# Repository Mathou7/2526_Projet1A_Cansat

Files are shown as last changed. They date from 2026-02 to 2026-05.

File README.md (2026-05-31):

# 2526_Projet1A_Cansat

## A Propos de la CanSat
Le concours CanSat, organisé chaque année dans le cadre du C’Space par le CNES et Planète Sciences, propose aux étudiants de concevoir, construire et faire voler un véritable mini-satellite de la taille d’une canette.
Lancé depuis un drone à environ 150 mètres d’altitude, le CanSat doit réaliser une mission scientifique ou technique en chute contrôlée, tout en respectant des contraintes strictes de taille, de masse et d’autonomie et en réalisant les missions imposées.
Ce concours permet aux étudiants d’aborder concrètement l’ensemble des étapes d’un projet spatial : conception système, intégration électronique, programmation embarquée, gestion de l’énergie et tests.

# L'équipe
- Marin.P
- Pierre-Antoine.R
- Lucas.G
- Arnaud.M
- Mathis.B.

## Liste des fonctionnalités
- Mesure de la pression grâce au baromètre
- Mesure de la distance grâce au TOF
- Utilisation d'un moteur pour actionner un mécanisme
- Prise de vidéo à l'aide de la caméra
- Interrupteur général permettant d'allumer et éteindre la canette

## Choix des composants
- Microcontroleur (stm32g431kbt)
- Baromètre (bnp581)
- Moteur brushless (GA12-N20)
- Centrale inertielle (abandonné) 
- Time of Lights (abandonné)
- Caméra (VC0706)
- Interrupteur

## PCB


PCB à quatre couches constitué de
- STM32G431KBT
- Régulateur 6.5-36V vers 5V
- Régulateur 5V vers 3.3V
- Driver Moteur
- Baromètre
- Interface Jack
- Interface Moteur
- Interface Bouton
- Interface Camera
- Connecteur ST

## Difficultés

Approvisionnement en composants
Nous n'avons pas reçu exactement les composants que l'on souhaitait au départ notamment la caméra qui devait enregistrer les images pendant la chute. Celle à laquelle nous avons eu accès transmet les images par onde radio, permettant de voir directement les images sur un écran extérieur à la canette.

Forme restrictive
La forme particulière du PCB imposée par le volume restreint de la canette et le système d'ouverture du parachute a constitué un frein considérable à la conception du PCB.

Code
Une étude détaillée du fonctionnement du baromètre a été nécessaire afin de coder les différentes fonctions permettant d'aboutir au calcul de l'altitude, ce qui a été très chronophage 

Conception de la canette
Le système d'ouverture du parachute a été le principal défi de conception nous forçant à modifier l'architecture de notre canette.

## Solutions trouvées

Les composants 
Pour la caméra nous avons trouvé une caméra avec un fonctionnement différent de celle initialement prévue.
Nous avons reçu le baromètre déjà soudé sur un PCB alors que nous avions demandé le baromètre seul, nous l'avons donc désoudé pour le resouder sur notre PCB.
En attendant la livraison du connecteur pour la batterie (JST-SH) nous avons soudé directement la batterie à l'interface prévue initialement pour le connecteur.

Conception de la canette 
Nous avons séparé notre canette en 2 espaces : une partie acceuillant le PCB et ses différents composants dont le moteur et une partie dans laquelle se trouve le parachute.
Le système d'ouverture fonctionne gràce à 2 goupilles qui maintiennent la partie contenant le parachute et la patie contenant le PCB ensemble. Ces 2 goupilles sont reliées par des fils au moteur qui en tournant va enrouler ces fils autour de son axe et les libérer. Le capuchon dans lequel se trouve le parachute va donc se détacher pour laisser le parachute sortir et se déployer. Le capuchon une fois détaché du reste de la canette reste relié à celle-ci via un autre fil nous permettant de respecter une exigeance imposée par le concours: aucune partie de la canette ne doit tomber au sol sans être ralentie.

## Partie Méca

Partie contenant le PCB et tout les éléments qui y sont reliés :


Opercule fermant la partie PCB qui maintient la partie parachute :


Corps du capuchon contenant le parachute : 


Opercule fermant le capuchon du parachute :


## Bilan des fonctionnalités

Test du bouton permettant d'allumer la LED

https://github.com/user-attachments/assets/89bd5818-fe06-4b41-a8be-61a60c13a220

Test du moteur

https://github.com/user-attachments/assets/85a999e9-10d9-4074-9609-f378fe4b467d

## Reflexion responsable 
Dans quelle mesure votre projet peut-il être intégré à des mesures d’adaptaton ou d’aténuaton du changement
climatque ?

Notre Cansat pourrait filmer un territoire pendant le largage et nous y montrer une évolution. Par exemple, face à une forêt, voir l'effet d'une déforestation ou d'une dégradation du territoire.

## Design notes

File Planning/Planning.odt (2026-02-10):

Planning

### Déjà fait :

Prototype de cannette utilisable : couvercle avec accroche parachute

parachute fabriquer(à améliorer possiblement)

idées pour ouvertures parachutes

carte STM déjà trouvé

composants choisi(à raffiner quand même pour les références)

### À venir :

-Semaine du 09/02-15/02 :

- Regrouper tous les composants
- Finaliser le schéma fonctionnel
- réussir à faire fonctionner les différents composants
  - obtenir des infos du baromètre, faire tourner les moteurs etc
- Avoir le nouveau modèle de la cansat (changements des tailles des 2 parties)

-Semaine du 16/02-22/02 :

- Si trop gourmand la semaine dernière : faire les tâches laissées en suspend
- voir le modèle du parachute ?
- Si possible faire un schématique complet
  - matériel exact et composant externe(résistance, condendateur, etc)
  - ne pas oublier de mettre des leds
- Kicad
  - finaliser schématique
- avoir un code fonctionnel pour le moteur
- tester l’un des 2 systèmes d’ouverture de parachute au moins

-Vacances du 23/02-08/03 :

- avoir un code qui regroupe le plus de composant sur Github
- Avancer le plus possible sur le routage

-Semaine du 02/03-08/03 :

- Faire vérifier notre Kicad par le professeur
- essayer d’avoir notre PCB
- se mettre d’accord sur un modèle finale de notre Cansat

-Semaine du 09/03-15/03

- Effectuer les premiers tests de notre code pour le baromètre et le TOF
- Faire une structure de Driver clean

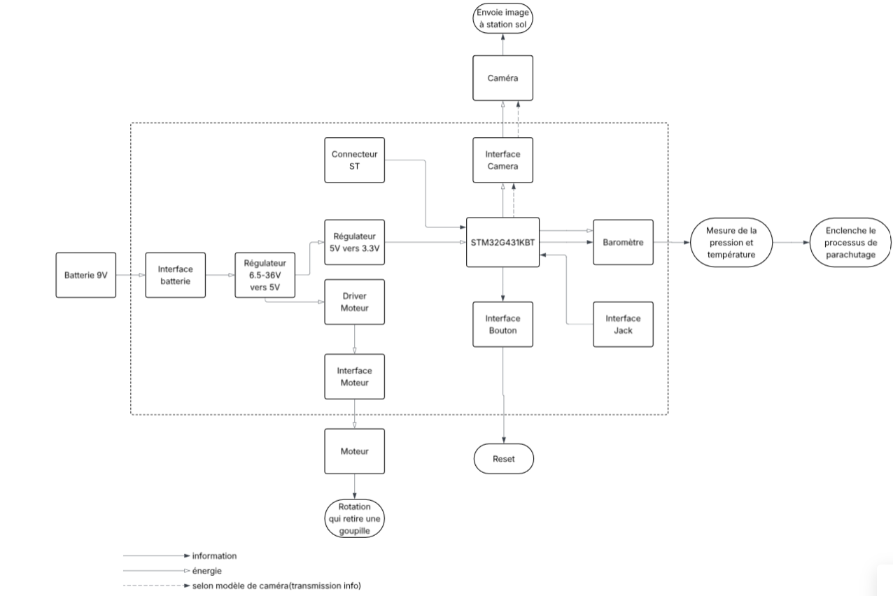
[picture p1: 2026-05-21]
Schéma bloc.png

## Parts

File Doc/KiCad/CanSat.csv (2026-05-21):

Reference | Qty | Value | DNP | Exclude from BOM | Exclude from Board | Footprint | Datasheet
C1,C2,C4,C10,C11 | 5 | 100nF |  |  |  | Capacitor_SMD:C_0603_1608Metric | ~
C5 | 1 | 2.2uF |  |  |  | Capacitor_SMD:C_0603_1608Metric | ~
C6,C12 | 2 | 10nF |  |  |  | Capacitor_SMD:C_0603_1608Metric | ~
C7 | 1 | 10uF |  |  |  | Capacitor_SMD:C_0603_1608Metric | ~
C8,C13,C14 | 3 | 1uF |  |  |  | Capacitor_SMD:C_0603_1608Metric | ~
C9 | 1 | 4.7uF |  |  |  | Capacitor_SMD:C_0603_1608Metric | ~
D1,D2,D3 | 3 | LED_Small |  |  |  | LED_SMD:LED_0603_1608Metric | ~
J1 | 1 | Conn_01x04 |  |  |  | Connector_JST:JST_XH_B4B-XH-A_1x04_P2.50mm_Vertical | ~
J2 | 1 | Conn_01x03 |  |  |  | Connector_JST:JST_SH_BM03B-SRSS-TB_1x03-1MP_P1.00mm_Vertical | ~
J4 | 1 | Conn_01x02 |  |  |  | Connector_JST:JST_XH_B2B-XH-A_1x02_P2.50mm_Vertical | ~
J5 | 1 | Conn_ST_STDC14 |  |  |  | Connector_PinHeader_1.27mm:PinHeader_2x07_P1.27mm_Vertical_SMD | https://www.st.com/content/ccc/resource/technical/document/user_manual/group1/99/49/91/b6/b2/3a/46/e5/DM00526767/files/DM00526767.pdf/jcr:content/translations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
J6 | 1 | Barrel_Jack_Switch |  |  |  | Connector_BarrelJack:BarrelJack_Wuerth_6941xx301002 | ~
R1,R5,R6 | 3 | 1k |  |  |  | Resistor_SMD:R_0603_1608Metric | ~
R2,R4 | 2 | 10k |  |  |  | Resistor_SMD:R_0603_1608Metric | ~
R3 | 1 | 200m |  |  |  | Resistor_SMD:R_0603_1608Metric | ~
SW3 | 1 | SW_Push |  |  |  | Button_Switch_THT:SW_PUSH_6mm_H5mm | ~
U1 | 1 | BMP581 |  |  |  | BMP581:BMP581
U2 | 1 | DRV8833PWP |  |  |  | Package_SO:HTSSOP-16-1EP_4.4x5mm_P0.65mm_EP3.4x5mm_Mask2.46x2.31mm_ThermalVias | http://www.ti.com/lit/ds/symlink/drv8833.pdf
U3 | 1 | STM32G431KBTx |  |  |  | Package_QFP:LQFP-32_7x7mm_P0.8mm | https://www.st.com/resource/en/datasheet/stm32g431kb.pdf
U4 | 1 | MIC5219-3.3YMM |  |  |  | Package_SO:MSOP-8_3x3mm_P0.65mm | http://ww1.microchip.com/downloads/en/DeviceDoc/MIC5219-500mA-Peak-Output-LDO-Regulator-DS20006021A.pdf
U5 | 1 | WPME-FDSM_SIP-3 |  |  |  | WPME-FDSM_SIP-3:WPME-FDSM_173010X78

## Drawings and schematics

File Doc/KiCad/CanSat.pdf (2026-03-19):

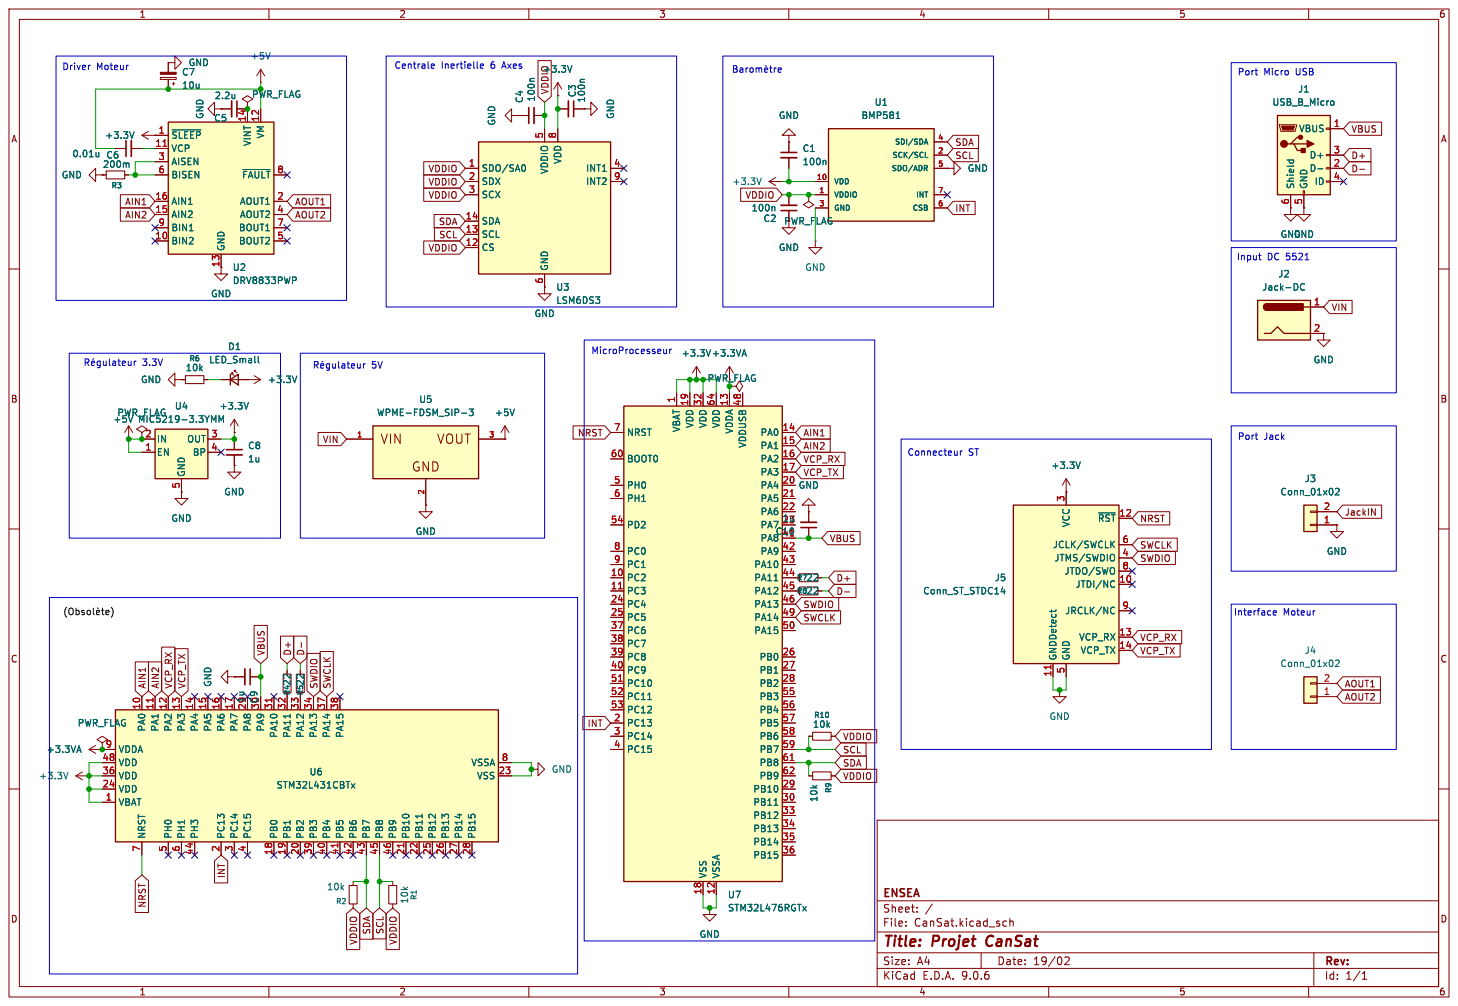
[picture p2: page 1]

Jack-DC GND VIN

1 VDD 19 VDD 32 VSS 18 VDD 64 VSSA 12 VDDA 13 VDDUSB 48 PA0 14 PA1 15 PA2 16 PA3 17 PA4 20 PA5 21 PA6 22 PA7 23 PA8 41 PA9 42 PA10 43 PA11 44 PA12 45 PA13 46 PA14 49 PA15 50 PB0 26 PB1 27 PB2 28 PB3 55 PB4 56 PB5 57 PB6 58 PB7 59 PB8 61 PB9 62 PB10 29 PB11 30 PB12 33 PB13 34 PB14 35 PB15 36 U7STM32L476RGTx C10

1 VDD 19 VDD 32 VSS 18 VDD 64 VSSA 12 VDDA 13 VDDUSB 48 PA0 14 PA1 15 PA2 16 PA3 17 PA4 20 PA5 21 PA6 22 PA7 23 PA8 41 PA9 42 PA10 43 PA11 44 PA12 45 PA13 46 PA14 49 PA15 50 PB0 26 PB1 27 PB2 28 PB3 55 PB4 56 PB5 57 PB6 58 PB7 59 PB8 61 PB9 62 PB10 29 PB11 30 PB12 33 PB13 34 PB14 35 PB15 36 C10

4 PB0 18 PB1 19 PB2 20 PB3 39 PB4 40 PB5 41 PB6 42 PB7 43 PB8 45 PB9 46 PB10 21 PB11 22 PB12 25 PB13 26 PB14 27 PB15 28 VBAT 1 VDD 24 VDD 36 VSS 23 VDD 48 VSSA 8 VDDA 9 PA0 10 PA1 11 PA2 12 PA3 13 PA4 14 PA5 15 PA6 16 PA7 17 PA8 29 PA9 30 PA10 31 PA11 32 PA12 33 PA13 34 PA14 37 PA15 381uC9 GND

4 PB0 18 PB1 19 PB2 20 PB3 39 PB4 40 PB5 41 PB6 42 PB7 43 PB8 45 PB9 46 PB10 21 PB11 22 PB12 25 PB13 26 PB14 27 PB15 28 VBAT 1 VDD 24 VDD 36 VSS 23 VDD 48 VSSA 8 VDDA 9 PA0 10 PA1 11 PA2 12 PA3 13 PA4 14 PA5 15 PA6 16 PA7 17 PA8 29 PA9 30 PA10 31 PA11 32 PA12 33 PA13 34 PA14 37 PA15 38 U6 STM32L431CBTx GND
PWR_FLAG

Id: 1/1 Title: Projet CanSat File: CanSat.kicad_sch Sheet: / ENSEA

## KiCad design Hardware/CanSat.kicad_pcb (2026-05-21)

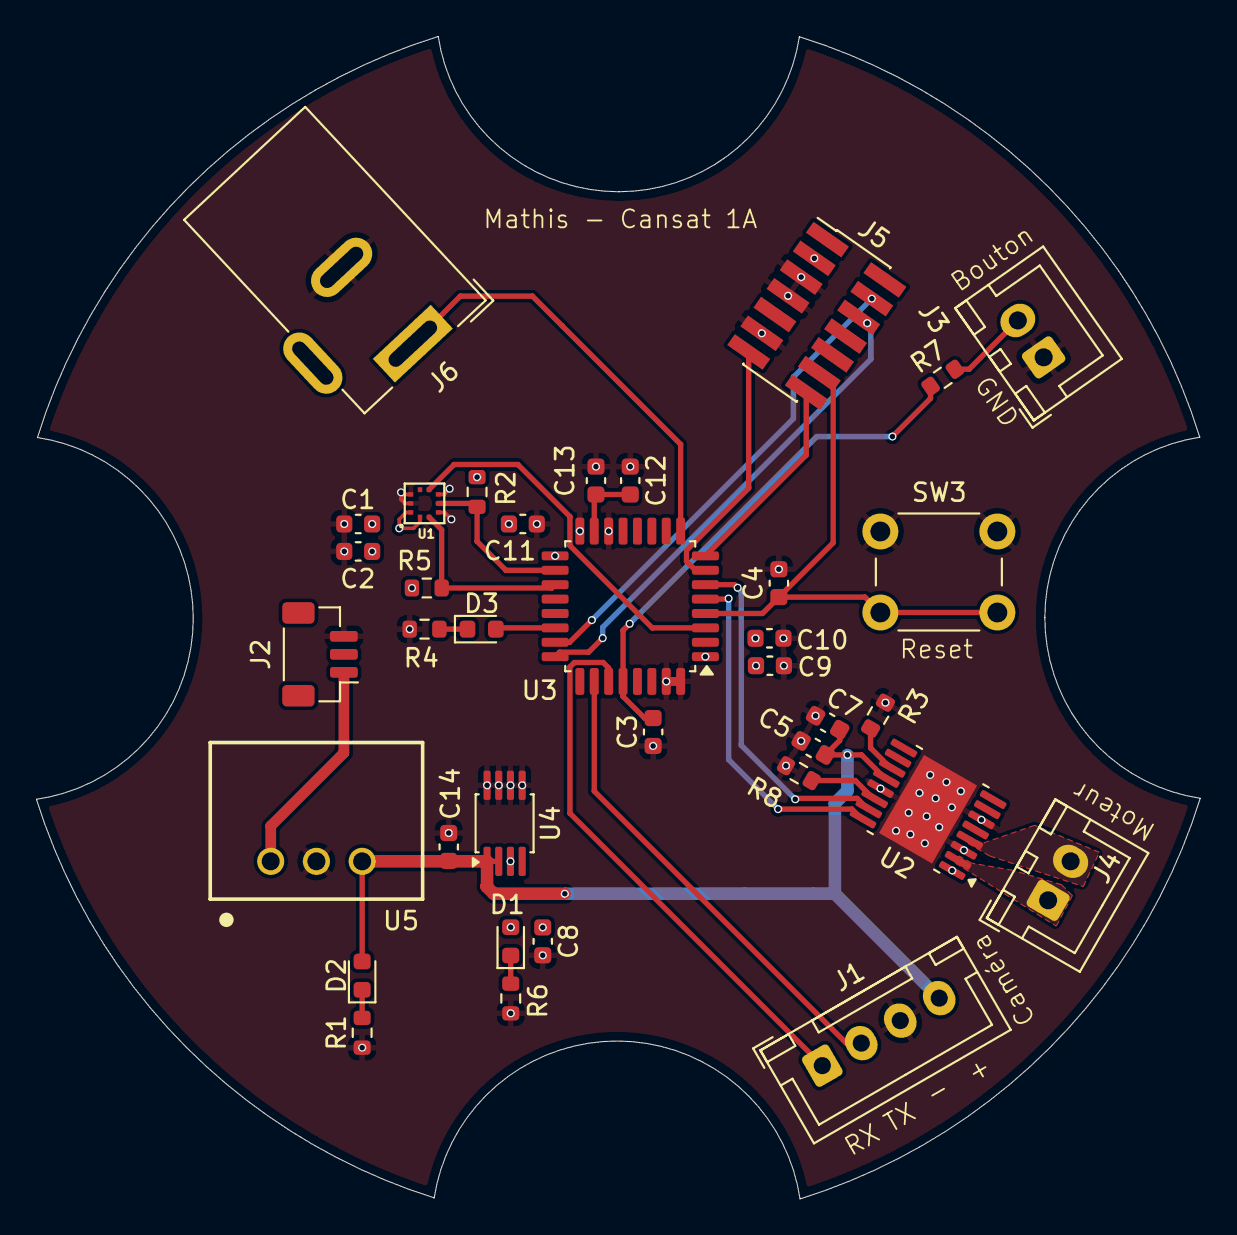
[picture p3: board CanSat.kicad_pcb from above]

Board: 4 copper layers, 64.7 x 64.6 mm, 36 parts (0 on the bottom side), 28 nets.

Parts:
C1, C2, C3, C4, C5, C10, C11: 100nF; C_0603_1608Metric
C7: 10uF; C_0603_1608Metric
C8, C13, C14: 1uF; C_0603_1608Metric
C9: 4.7uF; C_0603_1608Metric
C12: 10nF; C_0603_1608Metric
D1, D2, D3: LED_Small; LED_0603_1608Metric
J1: Conn_01x04; JST_XH_B4B-XH-A_1x04_P2.50mm_Vertical
J2: Conn_01x03; JST_SH_BM03B-SRSS-TB_1x03-1MP_P1.00mm_Vertical
J3, J4: Conn_01x02; JST_XH_B2B-XH-A_1x02_P2.50mm_Vertical
J5: Conn_ST_STDC14; PinHeader_2x07_P1.27mm_Vertical_SMD
J6: Barrel_Jack_Switch; BarrelJack_Wuerth_6941xx301002
R1, R5, R6: 1k; R_0603_1608Metric
R2, R3, R4, R8: 10k; R_0603_1608Metric
R7: 100; R_0603_1608Metric
SW3: SW_Push; SW_PUSH_6mm_H5mm
U1: BMP581
U2: DRV8833PWP; HTSSOP-16-1EP_4.4x5mm_P0.65mm_EP3.4x5mm_Mask2.46x2.31mm_The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
U3: STM32G431KBTx; LQFP-32_7x7mm_P0.8mm
U4: MIC5219-3.3YMM; MSOP-8_3x3mm_P0.65mm
U5: WPME-FDSM_SIP-3; WPME-FDSM_173010X78

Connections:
+3.3V: C1.2, C2.2, C8.1, C9.2, C10.2, C11.2, D1.2 (A), J5.3 (VCC), R2.2, R4.2, U1.1 (VDDIO), U1.10 (VDD), U2.1 (VREF), U3.1 (VDD), U3.17 (VDD), U4.3 (OUT)
+3.3VA: C12.2, C13.2, U3.15 (VDDA)
+5V: C5.2, C7.1, C14.1, D2.2 (A), J1.4, U2.12 (VM), U4.1 (EN), U4.2 (IN), U5.3
AIN1: U2.16 (AIN1), U3.5 (PA0)
AIN2: U2.15 (AIN2), U3.6 (PA1)
AOUT1: J4.1, U2.2 (AOUT1)
AOUT2: J4.2, U2.4 (AOUT2)
Bouton: C3.2, R7.1, U3.28 (PB5)
GND: C1.1, C2.1, C3.1, C4.2, C5.1, C7.2, C8.2, C9.1, C10.1, C11.1, C12.1, C13.1, C14.2, J1.3, J2.3, J3.1, J5.5 (GND), J5.7 (GND), J5.11 (GNDDetect), J6.2, R1.1, R3.2, R5.1, R6.1, R8.2, SW3.1, U1.3 (GND), U1.5 (SDO/ADR), U1.8 (GND), U1.9 (GND), U2.3 (GND), U2.6 (GND), U2.13 (GND), U2.17 (GND), U3.14 (VSSA), U3.16 (VSS), U3.31 (PB8), U3.32 (VSS), U4.5 (GND), U4.6 (GND), U4.7 (GND), U4.8 (GND), U5.2
INT: U1.6 (CSB), U3.3 (PF1)
JackIN: J6.1, U3.9 (PA4)
NRST: C4.1, J5.12 (~RST), SW3.2, U3.4 (PG10)
unnamed: D1.1 (K), R6.2
unnamed: D2.1 (K), R1.2
unnamed: D3.2 (A), U3.22 (PA12)
unnamed: D3.1 (K), R5.2
unnamed: J3.2, R7.2
unnamed: R8.1, U2.14 (AIPROPI)
unnamed: R3.1, U2.11 (BIPROPI)
RXCAM: J1.1, U3.27 (PB4)
SCL: R4.1, U1.2 (SCK/SCL), U3.19 (PA9)
SDA: R2.1, U1.4 (SDI/SDA), U3.18 (PA8)
SWCLK: J5.6 (JCLK/SWCLK), U3.24 (PA14)
SWDIO: J5.4 (JTMS/SWDIO), U3.23 (PA13)
TXCAM: J1.2, U3.26 (PB3)
VCP_RX: J5.13 (VCP_RX), U3.7 (PA2)
VCP_TX: J5.14 (VCP_TX), U3.8 (PA3)
VIN: J2.1, U5.1

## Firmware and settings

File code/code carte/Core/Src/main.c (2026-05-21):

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
/* Includes ------------------------------------------------------------------*/
#include "main.h"
/* USER CODE BEGIN Includes */
#include "stdbool.h"
#include "baro.h"
#include <stdio.h>
/* USER CODE END Includes */

I2C_HandleTypeDef hi2c1;

UART_HandleTypeDef huart2;

void SystemClock_Config(void);
static void MX_GPIO_Init(void);
static void MX_I2C1_Init(void);
static void MX_USART2_UART_Init(void);
/* USER CODE BEGIN PFP */
int __io_putchar(int ch)

	{
	HAL_UART_Transmit(&huart2, (uint8_t *)&ch, 1, HAL_MAX_DELAY);
	return ch;
	}

	int __io_getchar(void)
	{
	uint8_t ch = 0;
	__HAL_UART_CLEAR_OREFLAG(&huart2);
	HAL_UART_Receive(&huart2, (uint8_t *)&ch, 1, HAL_MAX_DELAY);
	HAL_UART_Transmit(&huart2, (uint8_t *)&ch, 1, HAL_MAX_DELAY);

	return ch;

	}
/* USER CODE END PFP */

/**
  * @brief  The application entry point.
  * @retval int
  */
int main(void)
{

  /* USER CODE BEGIN 1 */
static float alt;
  /* USER CODE END 1 */

  /* MCU Configuration--------------------------------------------------------*/

  /* Reset of all peripherals, Initializes the Flash interface and the Systick. */
  HAL_Init();

  /* Configure the system clock */
  SystemClock_Config();

  /* Initialize all configured peripherals */
  MX_GPIO_Init();
  MX_I2C1_Init();
  MX_USART2_UART_Init();
  /* USER CODE BEGIN 2 */
  BARO_Init();
  /* USER CODE END 2 */

  /* Infinite loop */
  /* USER CODE BEGIN WHILE */
	while (1)
  	{


			float * tab = ReadPressureTemp();
			float pression = tab[0];
			float altitude = altitute(pression);
			alt += altitude;



    /* USER CODE END WHILE */

    /* USER CODE BEGIN 3 */
	}
  /* USER CODE END 3 */
}

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


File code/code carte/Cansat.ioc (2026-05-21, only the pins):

Mcu.UserName=STM32L431CBTx
PA10.Signal=I2C1_SDA
PA2.Signal=USART2_TX
PA3.Signal=USART2_RX
PA9.Signal=I2C1_SCL
PB5.Signal=GPXTI5

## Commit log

2026-02-05 Update README Ajout fonctionnalités et composants
    Ajout du à propos, de la liste des fonctionnalités et du choix des composants
2026-02-19 Update Datasheets
    Ajout des datasheets de la STM, du baromètre, de la centrale inertielle et du driver moteur
2026-03-19 Ajout de datasheet
2026-03-19 Create code arduino caméra
2026-04-09 Ajout BOM
    Ajout de la fiche contenant tout les composants nécessaires au PCB
    [CanSat.csv]
2026-04-16 Upload Kicad files
    [CanSat.kicad_pcb, CanSat.kicad_sch]
2026-05-05 update code
    Rajout de l'entièreté du code du baromètre
2026-05-07 Update and rename camera.h to cam.h
2026-05-07 Update and rename camera.c to cam.c
2026-05-07 Amélioration du ReadME
    Updated project description and team members in README.md. Added details about the CanSat competition and PCB components.

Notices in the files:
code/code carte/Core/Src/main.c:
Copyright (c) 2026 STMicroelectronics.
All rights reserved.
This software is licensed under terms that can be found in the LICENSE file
